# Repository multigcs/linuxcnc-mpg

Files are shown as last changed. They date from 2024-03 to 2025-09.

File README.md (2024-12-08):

# MPG for LinuxCNC

work in progress !!

https://www.youtube.com/watch?v=mJ1qc-PS2gQ

DIY-MPG for LinuxCNC - wireless (https://www.youtube.com/watch?v=mJ1qc-PS2gQ "DIY-MPG for LinuxCNC - wireless")
DIY-MPG for LinuxCNC - hal tests (https://www.youtube.com/watch?v=hYcYCV4b4o4 "DIY-MPG for LinuxCNC - hal tests")

## TODO
- [x] espnow support (incl. dongle/bridge)
- [x] adding toggle support to the buttons (incl oneshot signals)
- [x] controling LED's and axis switching from python
- [x] transmitting only the diff of the encoder's
- [x] interception of connection problems
- [x] adding LIPO with wireless and USB charger
- [x] adding ADC to check LIPO voltage
- [ ] better GUI / maybe touch support (if i found a free usable pin)
- [ ] more values/halpins to display
- [ ] full hal examples

## BOM

| number | name | link |
| --- | --- | --- |
| 1 | S2 Mini V1.0.0 ESP32-S2 Modul | https://www.amazon.de/dp/B0CJHWD986 |
| 1 | 2.4Zoll TFT-Display (ILI9341) | https://www.amazon.de/dp/B0CC8V17GS |
| 1 | Emergency stop switch | https://www.amazon.de/dp/B08ZS8HZYV |
| 1 | rotary encoder | https://www.amazon.de/dp/B07MFVK8QT |
| 3 | rotary encoder with push button | https://www.amazon.de/dp/B096NYWY2M |
| 6 | 3mm LED | https://www.amazon.de/dp/B07Q1813PN |
| 14 | 12x12 momentary switch | https://www.amazon.de/dp/B07JBXS6RC |
| 1 | Resistor ~680Ohm | |

## PINS

| esp | func | tft | keys | leds | comment |
| --- | ---  | --- | ---  | ---  | --- |
| 14  | ADC  | | | | Batt-Voltage  |
| 33  | DC | D/C | | | |
| 34  | CS | CS | | | |
| 36  | SCK  | SCK | | | |
| 35  | MOSI | SDI | | | |
| 3V3 | | VCC | | | |
| GND | | GND | | | |
| 3V3 | | LED | | | |
| 3V3 | | RESET | | | |
| 10  | COL0 | | X | X | |
| 8 | COL1 | | X | X | |
| 6 | COL2 | | X | X | |
| 4 | COL3 | | X | X | |
| 2 | COL4 | | X | X | |
| 1 | COL5 | | X | X | |
| 7 | ROW0 | | X | | |
| 9 | ROW1 | | X | | |
| 5 | ROW2 | | X | | |
| 11  | ROW3 | | | X | |
| 13  | ENC1_A | | | | Jog-Wheel |
| 12  | ENC1_B | | | | Jog-Wheel |
| 16  | ENC2_A | | | | Feedrate |
| 17  | ENC2_B | | | | Feedrate |
| 18  | ENC3_A | | | | Rapid |
| 21  | ENC3_B | | | | Rapid |
| 38  | ENC4_A | | | | Spindle |
| 37  | ENC4_B | | | | Spindle |

## Compile and Load Firmware
you need a working platformio installation (https://platformio.org/install)
```
cd pendant
pio run --target upload
```

if you need a wireless connection (needs 2. ESP32S2):
```
cd dongle
pio run --target upload
```

## Install Hal-Component
```
sudo cp linuxcnc/mpg.py /usr/local/bin/mpg
sudo chmod 755 /usr/local/bin/mpg
``` 

## Hal-Pins

| name | dir | type |
| --- | --- | --- |
| mpg.axis.a.homed | IN | bit |
| mpg.axis.a.jog-counts | OUT | s32 |
| mpg.axis.a.pos | IN | float |
| mpg.axis.b.homed | IN | bit |
| mpg.axis.b.jog-counts | OUT | s32 |
| mpg.axis.b.pos | IN | float |
| mpg.axis.c.homed | IN | bit |
| mpg.axis.c.jog-counts | OUT | s32 |
| mpg.axis.c.pos | IN | float |
| mpg.axis.selected | IN | u32 |
| mpg.axis.x.homed | IN | bit |
| mpg.axis.x.jog-counts | OUT | s32 |
| mpg.axis.x.pos | IN | float |
| mpg.axis.y.homed | IN | bit |
| mpg.axis.y.jog-counts | OUT | s32 |
| mpg.axis.y.pos | IN | float |
| mpg.axis.z.homed | IN | bit |
| mpg.axis.z.jog-counts | OUT | s32 |
| mpg.axis.z.pos | IN | float |
| mpg.button.01 | OUT | bit |
| mpg.button.01-long | OUT | bit |
| mpg.button.01-long-not | OUT | bit |
| mpg.button.01-long-toggle | OUT | bit |
| mpg.button.01-long-toggle-not | OUT | bit |
| mpg.button.01-long-toggle-off | OUT | bit |
| mpg.button.01-long-toggle-on | OUT | bit |
| mpg.button.01-not | OUT | bit |
| mpg.button.01-toggle | OUT | bit |
| mpg.button.01-toggle-not | OUT | bit |
| mpg.button.01-toggle-off | OUT | bit |
| mpg.button.01-toggle-on | OUT | bit |
| mpg.button.01b | OUT | bit |
| mpg.button.01b-long | OUT | bit |
| mpg.button.01b-long-not | OUT | bit |
| mpg.button.01b-long-toggle | OUT | bit |
| mpg.button.01b-long-toggle-not | OUT | bit |
| mpg.button.01b-long-toggle-off | OUT | bit |
| mpg.button.01b-long-toggle-on | OUT | bit |
| mpg.button.01b-not | OUT | bit |
| mpg.button.01b-toggle | OUT | bit |
| mpg.button.01b-toggle-not | OUT | bit |
| mpg.button.01b-toggle-off | OUT | bit |
| mpg.button.01b-toggle-on | OUT | bit |
| mpg.button.02 | OUT | bit |
| mpg.button.02-long | OUT | bit |
| mpg.button.02-long-not | OUT | bit |
| mpg.button.02-long-toggle | OUT | bit |
| mpg.button.02-long-toggle-not | OUT | bit |
| mpg.button.02-long-toggle-off | OUT | bit |
| mpg.button.02-long-toggle-on | OUT | bit |
| mpg.button.02-not | OUT | bit |
| mpg.button.02-toggle | OUT | bit |
| mpg.button.02-toggle-not | OUT | bit |
| mpg.button.02-toggle-off | OUT | bit |
| mpg.button.02-toggle-on | OUT | bit |
| mpg.button.03 | OUT | bit |
| mpg.button.03-long | OUT | bit |
| mpg.button.03-long-not | OUT | bit |
| mpg.button.03-long-toggle | OUT | bit |
| mpg.button.03-long-toggle-not | OUT | bit |
| mpg.button.03-long-toggle-off | OUT | bit |
| mpg.button.03-long-toggle-on | OUT | bit |
| mpg.button.03-not | OUT | bit |
| mpg.button.03-toggle | OUT | bit |
| mpg.button.03-toggle-not | OUT | bit |
| mpg.button.03-toggle-off | OUT | bit |
| mpg.button.03-toggle-on | OUT | bit |
| mpg.button.04 | OUT | bit |
| mpg.button.04-long | OUT | bit |
| mpg.button.04-long-not | OUT | bit |
| mpg.button.04-long-toggle | OUT | bit |
| mpg.button.04-long-toggle-not | OUT | bit |
| mpg.button.04-long-toggle-off | OUT | bit |
| mpg.button.04-long-toggle-on | OUT | bit |
| mpg.button.04-not | OUT | bit |
| mpg.button.04-toggle | OUT | bit |
| mpg.button.04-toggle-not | OUT | bit |
| mpg.button.04-toggle-off | OUT | bit |
| mpg.button.04-toggle-on | OUT | bit |
| mpg.button.05 | OUT | bit |
| mpg.button.05-long | OUT | bit |
| mpg.button.05-long-not | OUT | bit |
| mpg.button.05-long-toggle | OUT | bit |
| mpg.button.05-long-toggle-not | OUT | bit |
| mpg.button.05-long-toggle-off | OUT | bit |
| mpg.button.05-long-toggle-on | OUT | bit |
| mpg.button.05-not | OUT | bit |
| mpg.button.05-toggle | OUT | bit |
| mpg.button.05-toggle-not | OUT | bit |
| mpg.button.05-toggle-off | OUT | bit |
| mpg.button.05-toggle-on | OUT | bit |
| mpg.button.06 | OUT | bit |
| mpg.button.06-long | OUT | bit |
| mpg.button.06-long-not | OUT | bit |
| mpg.button.06-long-toggle | OUT | bit |
| mpg.button.06-long-toggle-not | OUT | bit |
| mpg.button.06-long-toggle-off | OUT | bit |
| mpg.button.06-long-toggle-on | OUT | bit |
| mpg.button.06-not | OUT | bit |
| mpg.button.06-toggle | OUT | bit |
| mpg.button.06-toggle-not | OUT | bit |
| mpg.button.06-toggle-off | OUT | bit |
| mpg.button.06-toggle-on | OUT | bit |
| mpg.button.06b | OUT | bit |
| mpg.button.06b-long | OUT | bit |
| mpg.button.06b-long-not | OUT | bit |
| mpg.button.06b-long-toggle | OUT | bit |
| mpg.button.06b-long-toggle-not | OUT | bit |
| mpg.button.06b-long-toggle-off | OUT | bit |
| mpg.button.06b-long-toggle-on | OUT | bit |
| mpg.button.06b-not | OUT | bit |
| mpg.button.06b-toggle | OUT | bit |
| mpg.button.06b-toggle-not | OUT | bit |
| mpg.button.06b-toggle-off | OUT | bit |
| mpg.button.06b-toggle-on | OUT | bit |
| mpg.button.enc01 | OUT | bit |
| mpg.button.enc01-long | OUT | bit |
| mpg.button.enc01-long-not | OUT | bit |
| mpg.button.enc01-long-toggle | OUT | bit |
| mpg.button.enc01-long-toggle-not | OUT | bit |
| mpg.button.enc01-long-toggle-off | OUT | bit |
| mpg.button.enc01-long-toggle-on | OUT | bit |
| mpg.button.enc01-not | OUT | bit |
| mpg.button.enc01-toggle | OUT | bit |
| mpg.button.enc01-toggle-not | OUT | bit |
| mpg.button.enc01-toggle-off | OUT | bit |
| mpg.button.enc01-toggle-on | OUT | bit |
| mpg.button.enc02 | OUT | bit |
| mpg.button.enc02-long | OUT | bit |
| mpg.button.enc02-long-not | OUT | bit |
| mpg.button.enc02-long-toggle | OUT | bit |
| mpg.button.enc02-long-toggle-not | OUT | bit |
| mpg.button.enc02-long-toggle-off | OUT | bit |
| mpg.button.enc02-long-toggle-on | OUT | bit |
| mpg.button.enc02-not | OUT | bit |
| mpg.button.enc02-toggle | OUT | bit |
| mpg.button.enc02-toggle-not | OUT | bit |
| mpg.button.enc02-toggle-off | OUT | bit |
| mpg.button.enc02-toggle-on | OUT | bit |
| mpg.button.enc03 | OUT | bit |
| mpg.button.enc03-long | OUT | bit |
| mpg.button.enc03-long-not | OUT | bit |
| mpg.button.enc03-long-toggle | OUT | bit |
| mpg.button.enc03-long-toggle-not | OUT | bit |
| mpg.button.enc03-long-toggle-off | OUT | bit |
| mpg.button.enc03-long-toggle-on | OUT | bit |
| mpg.button.enc03-not | OUT | bit |
| mpg.button.enc03-toggle | OUT | bit |
| mpg.button.enc03-toggle-not | OUT | bit |
| mpg.button.enc03-toggle-off | OUT | bit |
| mpg.button.enc03-toggle-on | OUT | bit |
| mpg.button.estop | OUT | bit |
| mpg.button.estop-not | OUT | bit |
| mpg.button.estop-toggle | OUT | bit |
| mpg.button.estop-toggle-not | OUT | bit |
| mpg.button.estop-toggle-off | OUT | bit |
| mpg.button.estop-toggle-on | OUT | bit |
| mpg.button.sel01 | OUT | bit |
| mpg.button.sel01-long | OUT | bit |
| mpg.button.sel01-long-not | OUT | bit |
| mpg.button.sel01-long-toggle | OUT | bit |
| mpg.button.sel01-long-toggle-not | OUT | bit |
| mpg.button.sel01-long-toggle-off | OUT | bit |
| mpg.button.sel01-long-toggle-on | OUT | bit |
| mpg.button.sel01-not | OUT | bit |
| mpg.button.sel01-toggle | OUT | bit |
| mpg.button.sel01-toggle-not | OUT | bit |
| mpg.button.sel01-toggle-off | OUT | bit |
| mpg.button.sel01-toggle-on | OUT | bit |
| mpg.button.sel02 | OUT | bit |
| mpg.button.sel02-long | OUT | bit |
| mpg.button.sel02-long-not | OUT | bit |
| mpg.button.sel02-long-toggle | OUT | bit |
| mpg.button.sel02-long-toggle-not | OUT | bit |
| mpg.button.sel02-long-toggle-off | OUT | bit |
| mpg.button.sel02-long-toggle-on | OUT | bit |
| mpg.button.sel02-not | OUT | bit |
| mpg.button.sel02-toggle | OUT | bit |
| mpg.button.sel02-toggle-not | OUT | bit |
| mpg.button.sel02-toggle-off | OUT | bit |
| mpg.button.sel02-toggle-on | OUT | bit |
| mpg.button.sel03 | OUT | bit |
| mpg.button.sel03-long | OUT | bit |
| mpg.button.sel03-long-not | OUT | bit |
| mpg.button.sel03-long-toggle | OUT | bit |
| mpg.button.sel03-long-toggle-not | OUT | bit |
| mpg.button.sel03-long-toggle-off | OUT | bit |
| mpg.button.sel03-long-toggle-on | OUT | bit |
| mpg.button.sel03-not | OUT | bit |
| mpg.button.sel03-toggle | OUT | bit |
| mpg.button.sel03-toggle-not | OUT | bit |
| mpg.button.sel03-toggle-off | OUT | bit |
| mpg.button.sel03-toggle-on | OUT | bit |
| mpg.button.sel04 | OUT | bit |
| mpg.button.sel04-long | OUT | bit |
| mpg.button.sel04-long-not | OUT | bit |
| mpg.button.sel04-long-toggle | OUT | bit |
| mpg.button.sel04-long-toggle-not | OUT | bit |
| mpg.button.sel04-long-toggle-off | OUT | bit |
| mpg.button.sel04-long-toggle-on | OUT | bit |
| mpg.button.sel04-not | OUT | bit |
| mpg.button.sel04-toggle | OUT | bit |
| mpg.button.sel04-toggle-not | OUT | bit |
| mpg.button.sel04-toggle-off | OUT | bit |
| mpg.button.sel04-toggle-on | OUT | bit |
| mpg.button.sel05 | OUT | bit |
| mpg.button.sel05-long | OUT | bit |
| mpg.button.sel05-long-not | OUT | bit |
| mpg.button.sel05-long-toggle | OUT | bit |
| mpg.button.sel05-long-toggle-not | OUT | bit |
| mpg.button.sel05-long-toggle-off | OUT | bit |
| mpg.button.sel05-long-toggle-on | OUT | bit |
| mpg.button.sel05-not | OUT | bit |
| mpg.button.sel05-toggle | OUT | bit |
| mpg.button.sel05-toggle-not | OUT | bit |
| mpg.button.sel05-toggle-off | OUT | bit |
| mpg.button.sel05-toggle-on | OUT | bit |
| mpg.button.sel06 | OUT | bit |
| mpg.button.sel06-long | OUT | bit |
| mpg.button.sel06-long-not | OUT | bit |
| mpg.button.sel06-long-toggle | OUT | bit |
| mpg.button.sel06-long-toggle-not | OUT | bit |
| mpg.button.sel06-long-toggle-off | OUT | bit |
| mpg.button.sel06-long-toggle-on | OUT | bit |
| mpg.button.sel06-not | OUT | bit |
| mpg.button.sel06-toggle | OUT | bit |
| mpg.button.sel06-toggle-not | OUT | bit |
| mpg.button.sel06-toggle-off | OUT | bit |
| mpg.button.sel06-toggle-on | OUT | bit |
| mpg.jog-scale | OUT | float |
| mpg.led.01 | OUT | bit |
| mpg.led.02 | OUT | bit |
| mpg.led.03 | OUT | bit |
| mpg.led.04 | OUT | bit |
| mpg.led.05 | OUT | bit |
| mpg.led.06 | OUT | bit |
| mpg.machine.is-on | IN | bit |
| mpg.override.feed.counts | OUT | s32 |
| mpg.override.feed.value | IN | float |
| mpg.override.rapid.counts | OUT | s32 |
| mpg.override.rapid.value | IN | float |
| mpg.override.spindle.counts | OUT | s32 |
| mpg.override.spindle.value | IN | float |
| mpg.program.is-running | IN | bit |

## Hal-Configuration
this is for LinuxCNC >= 2.9

**please use your: custom_postgui.hal file**

### example1
``` 
loadusr -W mpg -d /dev/ttyACM0 -s

# MPG
#net iocontrol_0_emc-enable-in <= mpg.button.estop-not
#net iocontrol_0_emc-enable-in => iocontrol.0.emc-enable-in

net spindle_start <= mpg.button.01
net spindle_start => halui.spindle.0.start

net spindle_stop <= mpg.button.01b
net spindle_stop => halui.spindle.0.stop

setp joint.0.jog-vel-mode 1
setp joint.0.jog-scale 0.01
setp joint.0.jog-enable 1
setp axis.x.jog-vel-mode 1
setp axis.x.jog-scale 0.01
setp axis.x.jog-enable 1
net axis_x_jog-counts <= mpg.axis.x.jog-counts
net axis_x_jog-counts => axis.x.jog-counts
net axis_x_jog-counts => joint.0.jog-counts

setp joint.1.jog-vel-mode 1
setp joint.1.jog-scale 0.01
setp joint.1.jog-enable 1
setp axis.y.jog-vel-mode 1
setp axis.y.jog-scale 0.01
setp axis.y.jog-enable 1
net axis_y_jog-counts <= mpg.axis.y.jog-counts
net axis_y_jog-counts => axis.y.jog-counts
net xis_y_jog-counts => joint.1.jog-counts

net display_x halui.axis.x.pos-relative => mpg.axis.x.pos
net display_y halui.axis.y.pos-relative => mpg.axis.y.pos
net display_z halui.axis.z.pos-relative => mpg.axis.z.pos

setp halui.feed-override.scale 0.01
net feed-override <= mpg.override.feed.counts
net feed-override => halui.feed-override.counts

setp halui.rapid-override.scale 0.01
net rapid-override <= mpg.override.rapid.counts
net rapid-override => halui.rapid-override.counts

setp halui.spindle.0.override.scale 0.01
net spindle-override <= mpg.override.spindle.counts
net spindle-override => halui.spindle.0.override.counts

net override-feed-value <= halui.feed-override.value
net override-feed-value => mpg.override.feed.value

net override-rapid-value <= halui.rapid-override.value
net override-rapid-value => mpg.override.rapid.value

net override-spindle-value <= halui.spindle.0.override.value
net override-spindle-value => mpg.override.spindle.value

``` 

### example2

```
loadusr -W mpg -d /dev/ttyACM0 -s

#net rios.iocontrol_0_emc-enable-in <= mpg.button.estop-not
#net rios.iocontrol_0_emc-enable-in => iocontrol.0.emc-enable-in

net rios.x_select <= mpg.button.sel01
net rios.x_select => halui.axis.x.select
net rios.y_select <= mpg.button.sel02
net rios.y_select => halui.axis.y.select
net rios.z_select <= mpg.button.sel03
net rios.z_select => halui.axis.z.select

net rios.zero_x <= mpg.button.sel01-long
net rios.zero_x => halui.mdi-command-00
net rios.zero_y <= mpg.button.sel02-long
net rios.zero_y => halui.mdi-command-01
net rios.zero_z <= mpg.button.sel03-long
net rios.zero_z => halui.mdi-command-02

net rios.halui_machine_is-on => mpg.machine.is-on
net rios.halui_program_is-running => mpg.program.is-running

net rios.program_run <= mpg.button.01
net rios.program_run => halui.program.run
net rios.program_stop <= mpg.button.01-long
net rios.program_stop => halui.program.stop
net rios.program_pause <= mpg.button.01b
net rios.program_pause => halui.program.pause
net rios.program_resume <= mpg.button.01b-long
net rios.program_resume => halui.program.resume

net rios.x_homed <= joint.0.homed
net rios.x_homed => mpg.axis.x.homed
net rios.y_homed <= joint.1.homed
net rios.y_homed => mpg.axis.y.homed
net rios.z_homed <= joint.2.homed
net rios.z_homed => mpg.axis.z.homed

net rios.spindle_start <= mpg.button.02-long
net rios.spindle_start => halui.spindle.0.start

net rios.spindle_stop <= mpg.button.02
net rios.spindle_stop => halui.spindle.0.stop

net rios.jog-scale <= mpg.jog-scale
net rios.jog-scale => joint.0.jog-scale
net rios.jog-scale => axis.x.jog-scale
net rios.jog-scale => joint.1.jog-scale
net rios.jog-scale => axis.y.jog-scale

setp joint.0.jog-vel-mode 1
setp joint.0.jog-enable 1
setp axis.x.jog-vel-mode 1
setp axis.x.jog-enable 1
net rios.axis_x_jog-counts <= mpg.axis.x.jog-counts
net rios.axis_x_jog-counts => axis.x.jog-counts
net rios.axis_x_jog-counts => joint.0.jog-counts

setp joint.1.jog-vel-mode 1
setp joint.1.jog-enable 1
setp axis.y.jog-vel-mode 1
setp axis.y.jog-enable 1
net rios.axis_y_jog-counts <= mpg.axis.y.jog-counts
net rios.axis_y_jog-counts => axis.y.jog-counts
net rios.axis_y_jog-counts => joint.1.jog-counts

net display_x halui.axis.x.pos-relative => mpg.axis.x.pos
net display_y halui.axis.y.pos-relative => mpg.axis.y.pos
net display_z halui.axis.z.pos-relative => mpg.axis.z.pos

setp halui.feed-override.scale 0.01
net rios.feed-override <= mpg.override.feed.counts
net rios.feed-override => halui.feed-override.counts

setp halui.rapid-override.scale 0.01
net rios.rapid-override <= mpg.override.rapid.counts
net rios.rapid-override => halui.rapid-override.counts

setp halui.spindle.0.override.scale 0.01
net rios.spindle-override <= mpg.override.spindle.counts
net rios.spindle-override => halui.spindle.0.override.counts

net rios.override-feed-value <= halui.feed-override.value
net rios.override-feed-value => mpg.override.feed.value

net rios.override-rapid-value <= halui.rapid-override.value
net rios.override-rapid-value => mpg.override.rapid.value

net rios.override-spindle-value <= halui.spindle.0.override.value
net rios.override-spindle-value => mpg.override.spindle.value
```

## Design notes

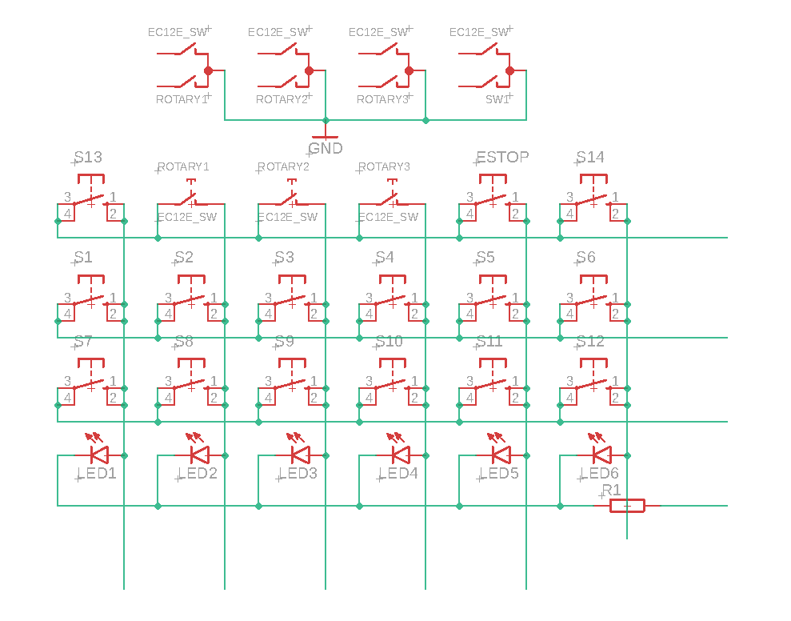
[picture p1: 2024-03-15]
pendant/matrix.png

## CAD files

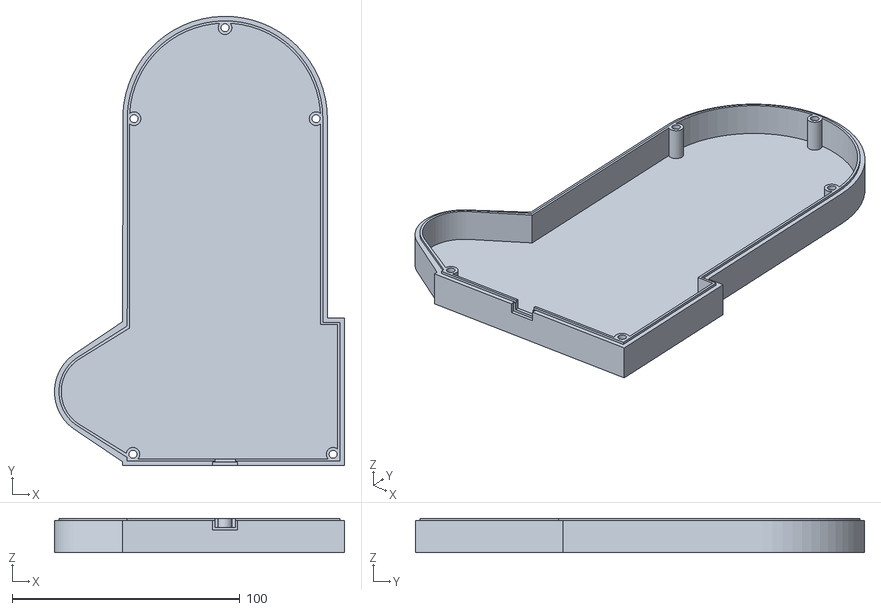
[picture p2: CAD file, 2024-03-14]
pendant/scad/cnc-pendant-bottom.stl
127.5 x 197.5 x 15.0

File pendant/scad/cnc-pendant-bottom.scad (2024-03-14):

$fn=63;


module encoder() {
    color([0.5, 0.5, 0.5, 0.5]) {
        cylinder(d=60, h=7);
        translate([0, 0, 7]) {
            cylinder(d1=60, d2=47, h=4);
        }
        cylinder(d=47, h=24);
        translate([16, 0, 0]) {
            cylinder(d=9, h=36);
        }
    }
}

module encoder_diff(off) {
    translate([0, 0, -10]) {
        cylinder(d=43, h=10.1);
    }

    translate([0, 0, -42]) {
        cylinder(d=61, h=40);
    }

    rotate([0, 0, 60+off]) {
        translate([0, 50.8/2, -10]) {
            cylinder(d=4, h=11);
        }
    }
    rotate([0, 0, 180+off]) {
        translate([0, 50.8/2, -10]) {
            cylinder(d=4, h=11);
        }
    }
    rotate([0, 0, -60+off]) {
        translate([0, 50.8/2, -10]) {
            cylinder(d=4, h=11);
        }
    }

}



module button() {
    translate([0, 0, -3.3/2]) {
        cube([12, 12, 3.3], center=true);
    }
    translate([0, 0, 3.5/2]) {
        cylinder(d=7, h=3.5, center=true);
    }

    translate([5.08/2, 12/2, -4.5]) {
        cylinder(d=1, h=4, center=true);
    }
    translate([5.08/2, -12/2, -4.5]) {
        cylinder(d=1, h=4, center=true);
    }
    translate([-5.08/2, 12/2, -4.5]) {
        cylinder(d=1, h=4, center=true);
    }
    translate([-5.08/2, -12/2, -4.5]) {
        cylinder(d=1, h=4, center=true);
    }
}

module button_diff() {
    translate([0, 0, -3.3/2]) {
        cube([12.5, 12.5, 3.3], center=true);
    }
    translate([0, 0, -9/2]) {
        cube([12.5, 12.5, 9.1], center=true);
    }

    translate([0, 0, 1/2]) {
        cube([10, 10, 1], center=true);
    }
    translate([0, 0, 5/2]) {
        cylinder(d=8, h=5, center=true);
    }

    translate([5.08/2, 12/2, -4.5]) {
        cylinder(d=2, h=6, center=true);
    }
    translate([5.08/2, -12/2, -4.5]) {
        cylinder(d=2, h=6, center=true);
    }
    translate([-5.08/2, 12/2, -4.5]) {
        cylinder(d=2, h=6, center=true);
    }
    translate([-5.08/2, -12/2, -4.5]) {
        cylinder(d=2, h=6, center=true);
    }
}


module rencoder() {
    translate([0, 0, -6.5/2]) {
        cube([12, 12, 6.5], center=true);
    }
    translate([0, 0, 6.5/2]) {
        cylinder(d=7, h=6.5, center=true);
    }
    translate([0, 0, 21/2]) {
        cylinder(d=6, h=21, center=true);
    }

    translate([5.08/2, 15/2, -7]) {
        cylinder(d=1, h=4, center=true);
    }
    translate([0, 15/2, -7]) {
        cylinder(d=1, h=4, center=true);
    }
    translate([5.08/2, -15/2, -7]) {
        cylinder(d=1, h=4, center=true);
    }
    translate([-5.08/2, 15/2, -7]) {
        cylinder(d=1, h=4, center=true);
    }
    translate([-5.08/2, -15/2, -7]) {
        cylinder(d=1, h=4, center=true);
    }
}

module rencoder_diff() {
    translate([0, 0, -6.5/2]) {
        cube([12.5, 12.5, 6.5], center=true);
    }
    translate([0, 0, -9/2]) {
        cube([12.5, 12.5, 9.1], center=true);
    }

    translate([0, 12/2, 0]) {
        cylinder(d=2, h=4, center=true);
    }

    translate([0, 0, 10/2]) {
        cylinder(d=7.5, h=10, center=true);
    }

    translate([5.08/2, 13/2, -4.5]) {
        cube([2, 4, 6], center=true);
    }
    translate([0, 13/2, -4.5]) {
        cube([2, 4, 6], center=true);
    }
    translate([5.08/2, -13/2, -4.5]) {
        cube([2, 4, 6], center=true);
    }
    translate([-5.08/2, 13/2, -4.5]) {
        cube([2, 4, 6], center=true);
    }
    translate([-5.08/2, -13/2, -4.5]) {
        cube([2, 4, 6], center=true);
    }
}

module led3mm(size) {
    cylinder(d=3, h=5.4, center=true);
    translate([0, 0, -2.21]) {
        cylinder(d=3.5, h=1, center=true);
    }
    translate([0, 2.54/2, -5.5]) {
        cylinder(d=1, h=7, center=true);
    }
    translate([0, -2.54/2, -5.5]) {
        cylinder(d=1, h=7, center=true);
    }
}

module led3mm_diff() {
    cylinder(d=3.3, h=10, center=true);

    translate([0, 0, -2.21]) {
        cylinder(d=3.5, h=1, center=true);
    }

    translate([0, 0, -6.75]) {
        cylinder(d=4, h=10, center=true);
    }

}


bd1 = 14.5;
bd1o = bd1/2;
bd1b = -3;
bd1e = 2;
bd1d = -2;

bd2 = 22;
bd2o = -bd2/2;
bd2b = -2;
bd2e = 3;
bd2d = -2;


ch = 15;



module case() {
    difference() {
        union() {
            hull() {
                translate([0, -120, -ch/2]) {
                    cube([90, 65, ch], center=true);
                }
                translate([0, 0, -ch]) {
                    cylinder(d=90, h=ch);
                }
            }
            translate([5, 0, 0]) {
                hull() {
                    translate([0, -120, -ch/2]) {
                        cube([95, 65, ch], center=true);
                    }
                    translate([-60, -120, -ch/2]) {
                        cylinder(d=40, h=ch, center=true);
                    }
                }
            }
        }

        hull() {
            translate([0, -120, -ch/2-2]) {
                cube([90-4, 65-4, ch], center=true);
            }
            translate([0, 0, -ch-2]) {
                cylinder(d=90-4, h=ch);
            }
        }
        translate([5, 0, 0]) {
            hull() {
                translate([0, -120, -ch/2-2]) {
                    cube([95-4, 65-4, ch], center=true);
                }
                translate([-60, -120, -ch/2-2]) {
                    cylinder(d=40-4, h=ch, center=true);
                }
            }
        }

    }

}


module case_bottom() {
    difference() {
        union() {
            hull() {
                translate([0, -120, -ch/2]) {
                    cube([90, 65, ch], center=true);
                }
                translate([0, 0, -ch]) {
                    cylinder(d=90, h=ch);
                }
            }
            translate([5, 0, 0]) {
                hull() {
                    translate([0, -120, -ch/2]) {
                        cube([95, 65, ch], center=true);
                    }
                    translate([-60, -120, -ch/2]) {
                        cylinder(d=40, h=ch, center=true);
                    }
                }
            }
        }

        hull() {
            translate([0, -120, -ch/2+2]) {
                cube([90-6, 65-6, ch], center=true);
            }
            translate([0, 0, -ch+2]) {
                cylinder(d=90-6, h=ch);
            }
        }
        translate([5, 0, 0]) {
            hull() {
                translate([0, -120, -ch/2+2]) {
                    cube([95-6, 65-6, ch], center=true);
                }
                translate([-60, -120, -ch/2+2]) {
                    cylinder(d=40-6, h=ch, center=true);
                }
            }
        }

        translate([0, 0, 14]) {
            case();
        }

        translate([40, 0, -16]) {
            cylinder(d=3.5, h=25);
        }
        translate([-40, 0, -16]) {
            cylinder(d=3.5, h=25);
        }
        translate([0, 40, -16]) {
            cylinder(d=3.5, h=25);
        }
        translate([47.5, -147.5, -16]) {
            cylinder(d=3.5, h=25);
        }
        translate([-40.5, -147.5, -16]) {
            cylinder(d=3.5, h=25);
        }

        translate([0, -150, -2]) {
            cube([9, 10, 4], center=true);
        }

        translate([0, -152, -2]) {
            cube([11, 2, 6], center=true);
        }


    }
    difference() {
        union() {
            translate([40, 0, -15]) {
                cylinder(d=6, h=15);
            }
            translate([-40, 0, -15]) {
                cylinder(d=6, h=15);
            }
            translate([0, 40, -15]) {
                cylinder(d=6, h=15);
            }
            translate([47.5, -147.5, -15]) {
                cylinder(d=6, h=15);
            }
            translate([-40.5, -147.5, -15]) {
                cylinder(d=6, h=15);
            }
        }

            translate([40, 0, -16]) {
                cylinder(d=3.5, h=25);
            }
            translate([-40, 0, -16]) {
                cylinder(d=3.5, h=25);
            }
            translate([0, 40, -16]) {
                cylinder(d=3.5, h=25);
            }
            translate([47.5, -147.5, -16]) {
                cylinder(d=3.5, h=25);
            }
            translate([-40.5, -147.5, -16]) {
                cylinder(d=3.5, h=25);
            }


    }
    

}








case_bottom();

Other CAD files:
pendant/scad/cnc-pendant.stl
pendant/scad/cnc-pendant.scad
pendant/scad/cnc-pendant.dxf

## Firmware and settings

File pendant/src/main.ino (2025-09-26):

#include <Wire.h> 
#include <ESPRotary.h>
#include <SPI.h>
#include <Adafruit_GFX.h>
#include <Adafruit_ILI9341.h>

#include <esp_now.h>
#include <esp_wifi.h>
#include <WiFi.h>


#define ADC 14
#define TFT_DC 33
#define TFT_CS 34
#define CLICKS_PER_STEP 4
#define PSTEP 32

SPIClass fspi = SPIClass(FSPI);
Adafruit_ILI9341 tft = Adafruit_ILI9341(&fspi, TFT_DC, TFT_CS);

ESPRotary r1;
ESPRotary r2;
ESPRotary r3;
ESPRotary r4;

uint8_t receiverAddress[] = {0x30, 0xAE, 0xA4, 0x7B, 0x79, 0x90};
uint8_t myAddress[] = {0x94, 0x3C, 0xC6, 0x33, 0x68, 0x98};
esp_now_peer_info_t peerInfo;

hw_timer_t *timer = NULL;

int col_pins[6] = {10, 8, 6, 4, 2, 1};
int row_pins[4] = {7, 9, 5, 11};

uint8_t sw_stat[3][6] = {
    {0, 0, 0, 0, 0, 0},
    {0, 0, 0, 0, 0, 0},
    {0, 0, 0, 0, 0, 0},
};

int32_t enc_diff[4] = {0, 0, 0, 0};

uint8_t overwrite_feed = 0;
char tmp_str[100];

struct rx_data_t {
    float pos[6];
    int16_t ow_feed;
    int16_t ow_rapid;
    int16_t ow_spindle;
    uint16_t leds;
    float jog_scale;
    float spindle_speed;
    int16_t stats;
    int8_t tool;
    int8_t aux;
};
const int rx_data_t_size = sizeof(rx_data_t);

uint8_t last_mode = 255;
rx_data_t last_values;
float last_batt_voltage = -1.0;



union rx_Data_t{
    rx_data_t values;
    byte data[rx_data_t_size];
};
rx_Data_t rx_data;  

struct tx_data_t {
    int16_t jog;
    int16_t ow_feed;
    int16_t ow_rapid;
    int16_t ow_spindle;
    uint32_t buttons;
};
const int tx_data_t_size = sizeof(tx_data_t);

union tx_Data_t{
    tx_data_t values;
    byte data[tx_data_t_size];
};
tx_Data_t tx_data;  


uint8_t update = 0;

void IRAM_ATTR handleLoop() {
    r1.loop();
    r2.loop();
    r3.loop();
    r4.loop();
}


void messageReceived(const uint8_t* macAddr, const uint8_t* incomingData, int len) {
    memcpy(&rx_data.data, incomingData, sizeof(rx_data.data));

    update_stats();

    esp_err_t result = esp_now_send(receiverAddress, (uint8_t *) &tx_data.data, sizeof(tx_data.data));
    if (result != ESP_OK) {
    }
}


void display_clear() {
    tft.fillScreen(ILI9341_BLACK);
    tft.setRotation(3);
    tft.setTextColor(ILI9341_WHITE, ILI9341_BLACK);

    tft.drawRect(1, 1, 202, 6 * PSTEP + 5 + 2, ILI9341_WHITE);
    tft.drawRect(2, 2, 200, 6 * PSTEP + 5, ILI9341_LIGHTGREY);

    tft.setTextSize(3);
    tft.setTextColor(ILI9341_RED, ILI9341_BLACK);
    tft.setCursor(10, 10 + 0 * PSTEP);
    tft.print("X: ");
    tft.setTextColor(ILI9341_GREEN, ILI9341_BLACK);
    tft.setCursor(10, 10 + 1 * PSTEP);
    tft.print("Y: ");
    tft.setTextColor(ILI9341_BLUE, ILI9341_BLACK);
    tft.setCursor(10, 10 + 2 * PSTEP);
    tft.print("Z: ");
    tft.setTextColor(ILI9341_YELLOW, ILI9341_BLACK);
    if ((rx_data.values.stats & (1<<0)) == 0) {
        tft.setCursor(10, 10 + 3 * PSTEP);
        tft.print("A: ");
        tft.setCursor(10, 10 + 4 * PSTEP);
        tft.print("B: ");
        tft.setCursor(10, 10 + 5 * PSTEP);
        tft.print("C: ");
    } else {
        tft.setTextSize(2);
        tft.setCursor(10, 10 + 4 * PSTEP + 4);
        tft.print("Speed:  ");
        tft.setCursor(10, 10 + 5 * PSTEP + 4);
        tft.print("Tool#:  ");
    }
    tft.setTextSize(3);
    tft.setCursor(10, 10 + 6 * PSTEP);

    uint8_t n = 0;
    for (n = 0; n < 6; n++) {
        last_values.pos[n] = rx_data.values.pos[n] + 1;
    }
    last_values.stats = rx_data.values.stats + 1;
    last_values.aux = rx_data.values.aux + 1;
    last_values.leds = rx_data.values.leds + 1;
    last_values.ow_feed = rx_data.values.ow_feed + 1;
    last_values.ow_rapid = rx_data.values.ow_rapid + 1;
    last_values.ow_spindle = rx_data.values.ow_spindle + 1;
    last_values.jog_scale = rx_data.values.jog_scale + 1;
    last_values.spindle_speed = rx_data.values.spindle_speed + 1;
    last_values.tool = rx_data.values.tool + 1;

}

void setup() {
    uint8_t n = 0;
    Serial.begin(115200);
    Serial.setTimeout(10);

    for (n = 0; n < 6; n++) {
        pinMode(col_pins[n], OUTPUT);
        digitalWrite(col_pins[n], 1);
    }
    pinMode(row_pins[0], INPUT_PULLUP);
    pinMode(row_pins[1], INPUT_PULLUP);
    pinMode(row_pins[2], INPUT_PULLUP);
    pinMode(row_pins[3], INPUT);

    fspi.begin(36, 37, 35, TFT_CS);
    tft.begin(78000000);

    display_clear();

    r1.begin(13, 12, CLICKS_PER_STEP);
    r2.begin(16, 17, CLICKS_PER_STEP);
    r3.begin(18, 21, CLICKS_PER_STEP);
    r4.begin(38, 37, CLICKS_PER_STEP);
    timer = timerBegin(0, 80, true);
    timerAttachInterrupt(timer, &handleLoop, true);
    timerAlarmWrite(timer, 100, true);
    timerAlarmEnable(timer);

    WiFi.mode(WIFI_STA);
    esp_wifi_set_mac(WIFI_IF_STA, myAddress);

    if (esp_now_init() == ESP_OK) {
        //Serial.println("ESPNow Init success");
    } else {
        //Serial.println("ESPNow Init fail");
        return;
    }
    esp_now_register_recv_cb(messageReceived);

    memcpy(peerInfo.peer_addr, receiverAddress, 6);
    peerInfo.channel = 0;
    peerInfo.encrypt = false;
    if (esp_now_add_peer(&peerInfo) != ESP_OK) {
        //Serial.println("Failed to add peer");
        return;
    }

}


void matrix_read() {
    uint8_t sw = 0;
    uint8_t n = 0;
    digitalWrite(row_pins[3], 0);
    pinMode(row_pins[3], INPUT);
    for (sw = 0; sw < 6; sw++) {
        for (n = 0; n < 6; n++) {
            pinMode(col_pins[n], INPUT);
        }
        pinMode(col_pins[sw], OUTPUT);
        digitalWrite(col_pins[sw], 0);
        sw_stat[0][sw] = digitalRead(row_pins[0]);
        sw_stat[1][sw] = digitalRead(row_pins[1]);
        sw_stat[2][sw] = digitalRead(row_pins[2]);
    }


    for (n = 0; n < 6; n++) {
        pinMode(col_pins[n], INPUT);
    }
    pinMode(row_pins[3], OUTPUT);
    digitalWrite(row_pins[3], 1);

    for (n = 0; n < 6; n++) {
        if ((rx_data.values.leds & (1<<n)) != 0) {
            pinMode(col_pins[n], OUTPUT);
            digitalWrite(col_pins[n], 0);
        } else {
            pinMode(col_pins[n], INPUT);
        }
    }

}


void update_stats() {
    uint8_t n = 0;
    for (n = 0; n < 6; n++) {
        if (rx_data.values.pos[n] > 99999.0) {
            rx_data.values.pos[n] = 99999.0;
        }
        if (rx_data.values.pos[n] > 99999.0) {
            rx_data.values.pos[n] = 99999.0;
        }
    }

    tx_data.values.jog = r1.getPosition();
    r1.resetPosition(0);


    tx_data.values.buttons = 0;
    for (n = 0; n < 6; n++) {
        if (sw_stat[0][n] == 0) {
            tx_data.values.buttons |= (1<<n);
        }
    }
    for (n = 0; n < 6; n++) {
        if (sw_stat[1][n] == 0) {
            tx_data.values.buttons |= (1<<(n+6));
        }
    }
    for (n = 0; n < 6; n++) {
        if (sw_stat[2][n] == 0) {
            tx_data.values.buttons |= (1<<(n+12));
        }
    }
}



void loop() {
    uint8_t sw = 0;
    uint8_t n = 0;
    uint8_t nr = 0;

    float batt_voltage = 0.0;


    for (n = 0; n < 100; n++) {
        batt_voltage += (float)analogRead(ADC);
    }
    batt_voltage = batt_voltage / 100.0 / 1500.0;


    matrix_read();
    tx_data.values.ow_feed = r2.getPosition();
    tx_data.values.ow_rapid = r3.getPosition();
    tx_data.values.ow_spindle = r4.getPosition();

    uint8_t rx_buffer[rx_data_t_size];
    uint8_t tx_buffer[tx_data_t_size];
    uint8_t rlen = Serial.readBytes(rx_buffer, rx_data_t_size);

    if (rlen == rx_data_t_size) {
        for (n = 0; n < rx_data_t_size; n++) {
            rx_data.data[n] = rx_buffer[n];
        }

        update_stats();

        for (n = 0; n < tx_data_t_size; n++) {
            tx_buffer[n] = tx_data.data[n];
        }
        Serial.write(tx_buffer, tx_data_t_size);

    }

    tft.setTextSize(2);
    tft.setTextColor(ILI9341_LIGHTGREY, ILI9341_BLACK);

    tft.setCursor(2, 5 + 4 * 45 + 25);
    if ((rx_data.values.stats & (1<<1)) != 0) {
        tft.setTextColor(ILI9341_GREEN, ILI9341_BLACK);
        tft.print("On  ");
    } else {
        tft.setTextColor(ILI9341_RED, ILI9341_BLACK);
        tft.print("Off ");
    }
    tft.setCursor(65, 5 + 4 * 45 + 25);
    if ((rx_data.values.stats & (1<<2)) != 0) {
        tft.setTextColor(ILI9341_GREEN, ILI9341_BLACK);
        tft.print("RUN  ");
    } else {
        tft.setTextColor(ILI9341_RED, ILI9341_BLACK);
        tft.print("STOP ");
    }

    tft.setTextColor(ILI9341_GREEN, ILI9341_BLACK);
    tft.setCursor(142, 5 + 4 * 45 + 25);
    if ((rx_data.values.stats & (1<<3)) != 0) {
        tft.print("AUTO ");
    } else if ((rx_data.values.stats & (1<<4)) != 0) {
        tft.print("MAN  ");
    } else if ((rx_data.values.stats & (1<<5)) != 0) {
        tft.print("MDI  ");
    } else {
        tft.setTextColor(ILI9341_RED, ILI9341_BLACK);
        tft.print(" --  ");
    }

    uint8_t num_axis = 6;
    // display-mode
    if ((rx_data.values.stats & (1<<0)) == 0) {
        if (last_mode != 0) {
            last_mode = 0;
            display_clear();
        }
        // axis positions and homed
        tft.setTextSize(3);
        for (n = 0; n < 6; n++) {
            if (last_values.leds != rx_data.values.leds || last_values.pos[n] != rx_data.values.pos[n]) {
                last_values.pos[n] = rx_data.values.pos[n];
                if ((rx_data.values.leds & (1<<(8+n))) != 0) {
                    tft.setTextColor(ILI9341_GREEN, ILI9341_BLACK);
                } else {
                    tft.setTextColor(ILI9341_RED, ILI9341_BLACK);
                }
                tft.setCursor(50, 10 + n * PSTEP);
                sprintf(tmp_str, "%08.2f", rx_data.values.pos[n]);
                tft.print(tmp_str);
            }
            last_values.leds = rx_data.values.leds;
        }
    } else {
        if (last_mode != 1) {
            last_mode = 1;
            display_clear();
        }
        // axis positions and homed
        tft.setTextSize(3);
        for (n = 0; n < 3; n++) {
            if (last_values.leds != rx_data.values.leds || last_values.pos[n] != rx_data.values.pos[n]) {
                last_values.pos[n] = rx_data.values.pos[n];
                if ((rx_data.values.leds & (1<<(8+n))) != 0) {
                    tft.setTextColor(ILI9341_GREEN, ILI9341_BLACK);
                } else {
                    tft.setTextColor(ILI9341_RED, ILI9341_BLACK);
                }
                tft.setCursor(50, 10 + n * PSTEP);
                sprintf(tmp_str, "%08.2f", rx_data.values.pos[n]);
                tft.print(tmp_str);
            }
            last_values.leds = rx_data.values.leds;
        }

        // coolant mist/flood
        tft.setTextSize(1);
        tft.setCursor(90, 10 + 5 * PSTEP - 1);
        if ((rx_data.values.stats & (1<<6)) != 0) {
            tft.setTextColor(ILI9341_GREEN, ILI9341_BLACK);
        } else {
            tft.setTextColor(ILI9341_DARKGREY, ILI9341_BLACK);
        }
        tft.print("mist");

        tft.setCursor(90, 10 + 5 * PSTEP + 10);
        if ((rx_data.values.stats & (1<<7)) != 0) {
            tft.setTextColor(ILI9341_GREEN, ILI9341_BLACK);
        } else {
            tft.setTextColor(ILI9341_DARKGREY, ILI9341_BLACK);
        }
        tft.print("flood");

        // speed
        tft.setTextSize(3);
        tft.setTextColor(ILI9341_GREEN, ILI9341_BLACK);
        if (last_values.spindle_speed != rx_data.values.spindle_speed) {
            tft.setCursor(105, 10 + 4 * PSTEP);
            sprintf(tmp_str, "%05.0f", rx_data.values.spindle_speed * 60.0);
            tft.print(tmp_str);
        }
        last_values.spindle_speed = rx_data.values.spindle_speed;
        // tool
        if (last_values.tool != rx_data.values.tool) {
            tft.setCursor(105, 10 + 5 * PSTEP);
            sprintf(tmp_str, "  %03.0f", (float)(rx_data.values.tool));
            tft.print(tmp_str);
        }
        last_values.tool = rx_data.values.tool;
    }

    if (last_values.ow_feed != rx_data.values.ow_feed) {
        last_values.ow_feed = rx_data.values.ow_feed;
        nr = 0;
        tft.setTextSize(1);
        tft.setTextColor(ILI9341_YELLOW, ILI9341_BLACK);
        tft.setCursor(215, 5 + nr * 47 + 2);
        tft.print("Feed:");
        tft.setTextSize(3);
        tft.setTextColor(ILI9341_BLUE, ILI9341_BLACK);
        tft.setCursor(230+16, 5 + nr * 45 + 25);
        sprintf(tmp_str, "%3i%%", rx_data.values.ow_feed);
        tft.print(tmp_str);
    }

    if (last_values.ow_rapid != rx_data.values.ow_rapid) {
        last_values.ow_rapid = rx_data.values.ow_rapid;
        nr = 1;
        tft.setTextSize(1);
        tft.setTextColor(ILI9341_YELLOW, ILI9341_BLACK);
        tft.setCursor(215, 5 + nr * 47 + 2);
        tft.print("Rapid:");
        tft.setTextSize(3);
        tft.setTextColor(ILI9341_BLUE, ILI9341_BLACK);
        tft.setCursor(230+16, 5 + nr * 45 + 25);
        sprintf(tmp_str, "%3i%%", rx_data.values.ow_rapid);
        tft.print(tmp_str);
    }

    if (last_values.ow_spindle != rx_data.values.ow_spindle) {
        last_values.ow_spindle = rx_data.values.ow_spindle;
        nr = 2;
        tft.setTextSize(1);
        tft.setTextColor(ILI9341_YELLOW, ILI9341_BLACK);
        tft.setCursor(215, 5 + nr * 47 + 2);
        tft.print("Spindle:");
        tft.setTextSize(3);
        tft.setTextColor(ILI9341_BLUE, ILI9341_BLACK);
        tft.setCursor(230+16, 5 + nr * 45 + 25);
        sprintf(tmp_str, "%3i%%", rx_data.values.ow_spindle);
        tft.print(tmp_str);
    }

    if (last_batt_voltage != batt_voltage) {
        last_batt_voltage != batt_voltage;
        nr = 3;
        tft.setTextSize(1);
        tft.setTextColor(ILI9341_YELLOW, ILI9341_BLACK);
        tft.setCursor(215, 5 + nr * 47 + 2);
        tft.print("BATT:");
        tft.setTextSize(3);
        tft.setTextColor(ILI9341_BLUE, ILI9341_BLACK);
        tft.setCursor(230, 5 + nr * 45 + 25);
        sprintf(tmp_str, "%0.2fV", batt_voltage);
        tft.print(tmp_str);
    }

    if (last_values.jog_scale != rx_data.values.jog_scale) {
        last_values.jog_scale = rx_data.values.jog_scale;
        nr = 4;
        tft.setTextSize(1);
        tft.setTextColor(ILI9341_YELLOW, ILI9341_BLACK);
        tft.setCursor(215, 5 + nr * 47 + 2);
        tft.print("Jog-Scale:");
        tft.setTextSize(3);
        tft.setTextColor(ILI9341_BLUE, ILI9341_BLACK);
        tft.setCursor(230, 5 + nr * 45 + 25);
        sprintf(tmp_str, "%04.3f", rx_data.values.jog_scale);
        tft.print(tmp_str);
    }



    delay(5);

}

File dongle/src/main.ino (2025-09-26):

#include <esp_now.h>
#include <esp_wifi.h>
#include <WiFi.h>

#define LED_PIN 15

uint8_t receiverAddress[] = {0x94, 0x3C, 0xC6, 0x33, 0x68, 0x98};
uint8_t myAddress[] = {0x30, 0xAE, 0xA4, 0x7B, 0x79, 0x90};

volatile uint8_t rx_ok = 0;

struct rx_data_t {
    float pos[6];
    int16_t ow_feed;
    int16_t ow_rapid;
    int16_t ow_spindle;
    int16_t leds;
    float jog_scale;
    float spindle_speed;
    int16_t stats;
    int8_t tool;
    int8_t aux;
};
const int rx_data_t_size = sizeof(rx_data_t);

union rx_Data_t{
    rx_data_t values;
    byte data[rx_data_t_size];
};
volatile rx_Data_t rx_data;  

struct tx_data_t {
    int16_t jog;
    int16_t ow_feed;
    int16_t ow_rapid;
    int16_t ow_spindle;
    uint32_t buttons;
};
const int tx_data_t_size = sizeof(tx_data_t);

union tx_Data_t{
    tx_data_t values;
    byte data[tx_data_t_size];
};
tx_Data_t tx_data;

struct ltx_data_t {
    int16_t analog[3];
    uint8_t buttons;
    uint8_t stats;
};
const int ltx_data_t_size = sizeof(ltx_data_t);

union ltx_Data_t{
    ltx_data_t values;
    byte data[ltx_data_t_size];
};
ltx_Data_t ltx_data;


esp_now_peer_info_t peerInfo;

void messageSent(const uint8_t *macAddr, esp_now_send_status_t status) {
    if (status == ESP_NOW_SEND_SUCCESS) {
    }
}

void messageReceived(const uint8_t* macAddr, const uint8_t* incomingData, int len) {
    memcpy(&tx_data.data, incomingData, sizeof(tx_data.data));
    rx_ok = 1;
}

void setup() {
    pinMode(LED_PIN, OUTPUT);
    digitalWrite(LED_PIN, 1);
    pinMode(33, INPUT_PULLUP);

    Serial.begin(115200);
    // delay(1000); // uncomment if your serial monitor is empty
    WiFi.mode(WIFI_STA);
    esp_wifi_set_mac(WIFI_IF_STA, myAddress);


    if (esp_now_init() == ESP_OK) {
        //Serial.println("ESPNow Init success");
    } else {
        //Serial.println("ESPNow Init fail");
        return;
    }

    esp_now_register_send_cb(messageSent);
    esp_now_register_recv_cb(messageReceived);
    memcpy(peerInfo.peer_addr, receiverAddress, 6);
    peerInfo.channel = 0;
    peerInfo.encrypt = false;
    if (esp_now_add_peer(&peerInfo) != ESP_OK) {
        //Serial.println("Failed to add peer");
        return;
    }
}

uint8_t response = 0;
uint8_t rx_start_pos = 0;
void loop() {
    uint8_t csum = 0;
    uint8_t n = 0;
    uint8_t rx_buffer[rx_data_t_size];
    uint8_t tx_buffer[tx_data_t_size + ltx_data_t_size + 5];

    tx_buffer[0] = 123;
    tx_buffer[1] = 234;
    tx_buffer[2] = 222;
    tx_buffer[3] = 111;

    if (rx_ok == 1) {
        rx_ok = 0;
        digitalWrite(LED_PIN, 1);
        for (n = 0; n < tx_data_t_size; n++) {
            tx_buffer[4 + n] = tx_data.data[n];
        }
    } else {
        digitalWrite(LED_PIN, 0);
    }

    while (Serial.available() > 0) {
        uint8_t c = Serial.read();
        //Serial.print("< ");
        //Serial.println(c);

        if (rx_start_pos == 0 && c == 99) {
            rx_start_pos = 1;
            //Serial.println("#1");
        } else if (rx_start_pos == 1 && c == 18) {
            rx_start_pos = 2;
            //Serial.println("#2");
        } else if (rx_start_pos == 2 && c == 27) {
            rx_start_pos = 3;
            //Serial.println("#3");
        } else if (rx_start_pos == 3 && c == 36) {
            rx_start_pos = 0;
            uint8_t rlen = Serial.readBytes(rx_buffer, rx_data_t_size);
            if (rlen == rx_data_t_size) {
                csum = 0;
                for (n = 0; n < rx_data_t_size; n++) {
                    rx_data.data[n] = rx_buffer[n];
                    csum += rx_buffer[n];
                }
                c = Serial.read();
                if (c == csum) {
                    esp_err_t result = esp_now_send(receiverAddress, (uint8_t *) &rx_data.data, sizeof(rx_data.data));
                    if (result != ESP_OK) {
                    }
                }
                response = 1;
            }
        } else {
            rx_start_pos = 0;
            Serial.println("sync error");
        }
    }
    if (response == 1) {
        response = 0;
        analogSetClockDiv(40);
        uint32_t adc0 = 0;
        uint32_t adc1 = 0;
        uint32_t adc2 = 0;
        for (n = 0; n < 100; n++) {
            adc0 += analogRead(35);
            adc1 += analogRead(34);
            adc2 += analogRead(39);
        }
        ltx_data.values.analog[0] = adc0 / 100;
        ltx_data.values.analog[1] = adc1 / 100;
        ltx_data.values.analog[2] = adc2 / 100;
        ltx_data.values.buttons = 0;
        if (digitalRead(33) == 0) {
            ltx_data.values.buttons |= (1<<0);
        }
        
        for (n = 0; n < ltx_data_t_size; n++) {
            tx_buffer[4 + tx_data_t_size + n] = ltx_data.data[n];
        }

        csum = 0;
        for (n = 0; n < 4 + tx_data_t_size + ltx_data_t_size; n++) {
            csum += tx_buffer[n];
        }
        tx_buffer[4 + tx_data_t_size + ltx_data_t_size] = csum;
        Serial.write(tx_buffer, tx_data_t_size + ltx_data_t_size + 5);
    }

    delay(1);

}

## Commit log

2024-03-14 initial release
    [cnc-pendant-bottom.scad, cnc-pendant-bottom.stl, cnc-pendant.scad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]
2024-03-15 adding matrix schematic
2024-03-15 restructure folders
    [cnc-pendant-bottom.scad, cnc-pendant-bottom.stl, cnc-pendant.scad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]
2024-03-15 check serial connection / reconnect on error
    [mpg.py]
2024-03-15 adding button long press support
2024-03-16 adding adc messurement
2024-03-17 dongle status LED
2024-06-26 adding pendant pcb-test firmware
2024-06-28 fixing pcb-test jog
2025-09-26 dxf front
    [cnc-pendant.dxf]
